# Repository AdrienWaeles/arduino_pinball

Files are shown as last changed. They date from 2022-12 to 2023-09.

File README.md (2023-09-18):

Dans le cadre des cours de robotique de 2ème année de classe préparatoire intégrée à Polytech Nice Sophia. Nous avons conçu et fabriqué un flipper de A à Z entièrement contrôlé par une carte Arduino.  

Ce GitHub rassemble nos rapports d'avancée hebdomadaire ainsi que tous les fichiers créés pour concevoir ce flipper.

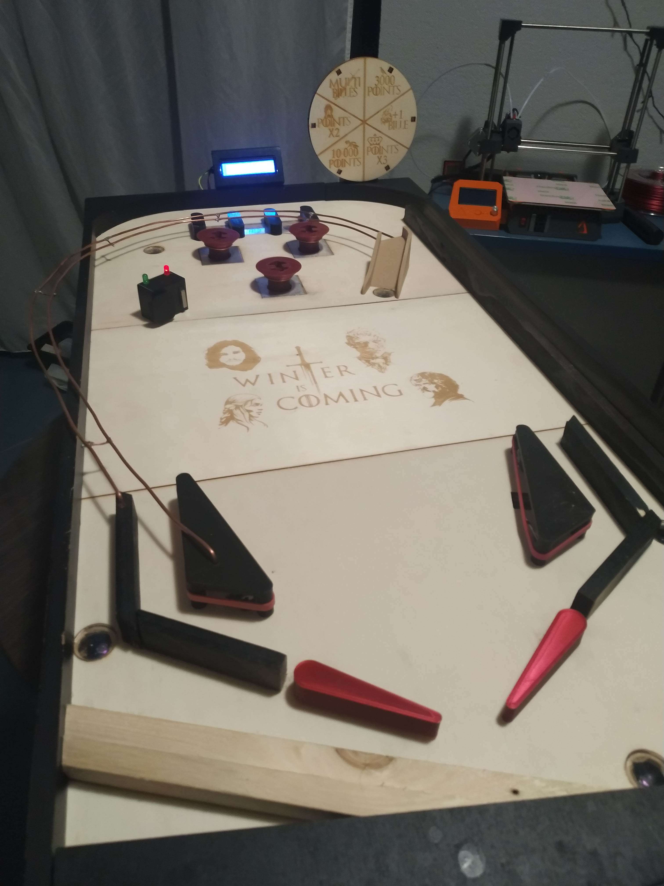
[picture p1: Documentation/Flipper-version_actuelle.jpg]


**Vidéo de présentation du projet** : https://youtu.be/dcDQBHgphmI

Cette première version a dû être réalisée dans un délai très court (moins de 3 mois) en pleine année scolaire. Ainsi nous avons du nous focaliser sur l'essentiel, mais ce projet a été conçu dès le début pour être évolutif et bénificiera d'améliorations prochainement.

Projet réalisé par Abderrahmane Redha et Waeles-Devaux Adrien.

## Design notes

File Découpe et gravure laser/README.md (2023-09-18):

Vous trouverez ici, tous les fichiers vectoriels (formmat SVG) conçus pour la découpeuse laser afin de réaliser les bordures et planches de jeu du Flipper.

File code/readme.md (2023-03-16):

Voici tous les programmes réalisés sur Arduino IDE pour tester nos différents éléments et la dernière version complète du jeu

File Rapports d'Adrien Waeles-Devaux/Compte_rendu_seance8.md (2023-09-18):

**Avant la séance :**

Nous avons profité des vacances pour passer quelques jours au Fablab afin d’assembler notre flipper. 
Pour cela avec l’aide de Frédéric Juan du Fablab nous avons commencé par coller les 3 fines planches sur la grande planche de jeu afin d’avoir l’emplacement de tous les trous à percer. Puis nous avons vissé toutes les bordures précédemment fabriquées.

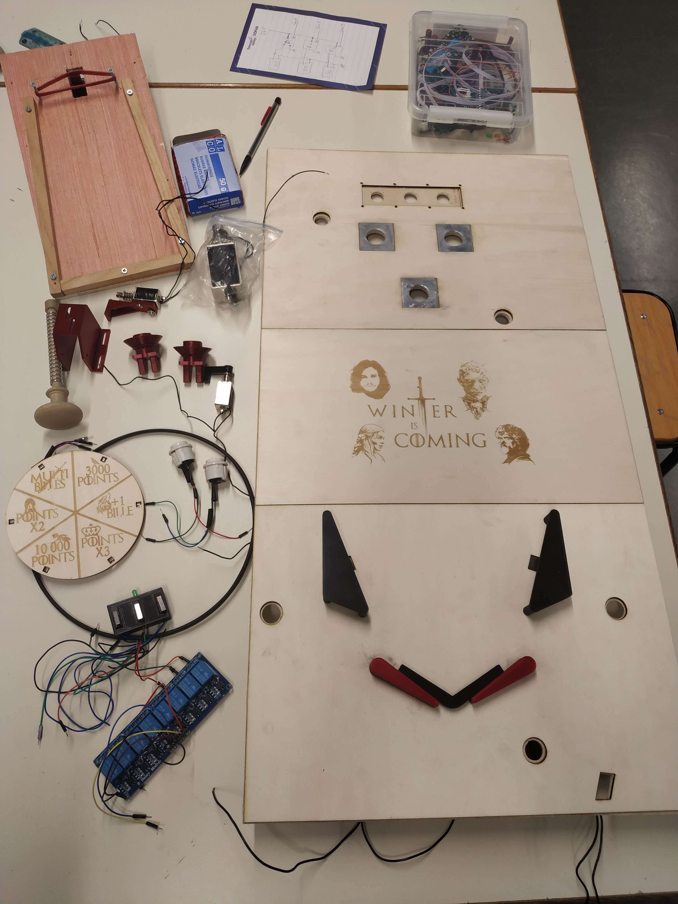
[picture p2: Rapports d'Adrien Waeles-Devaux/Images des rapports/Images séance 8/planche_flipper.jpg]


Pour déterminer l’inclinaison optimale de notre pinball nous avons utilisé un inclinomètre numérique. La plupart des pinball ont une inclinaison comprise entre 3° et 6°, après avoir testé différentes inclinaisons avec des cales de bois, nous avons choisi une inclinaison de 4°. J’ai ensuite mesuré et dessiné au crayon le support permettant d'incliner le pinball sur des morceaux de bois afin de les découper.

Il a fallu également effectuer un trou dans la bordure inférieure pour y insérer la poignée (modélisée en 3d avec un filetage pour pouvoir la démonter afin de l’insérer dans le trou). Cependant étant donné la force exercée par le ressort sur la bordure nous avons dû la renforcer par un morceau de bois plus haut à cet endroit.

Pour ramener la bille dans la zone de lancement lorsqu’elle est perdue par le joueur, nous avons vissé un solénoïde sous la planche et attaché à celui- ci un bras imprimé en 3D que j’ai modélisé. Ainsi lorsque celui-ci s'activera (donc quand la bille sera détectée par un capteur infrarouge de sortie de jeu), le bras du solénoïde poussera la bille pour l’envoyer au-dessus de la tige de la poignée de lancement. 

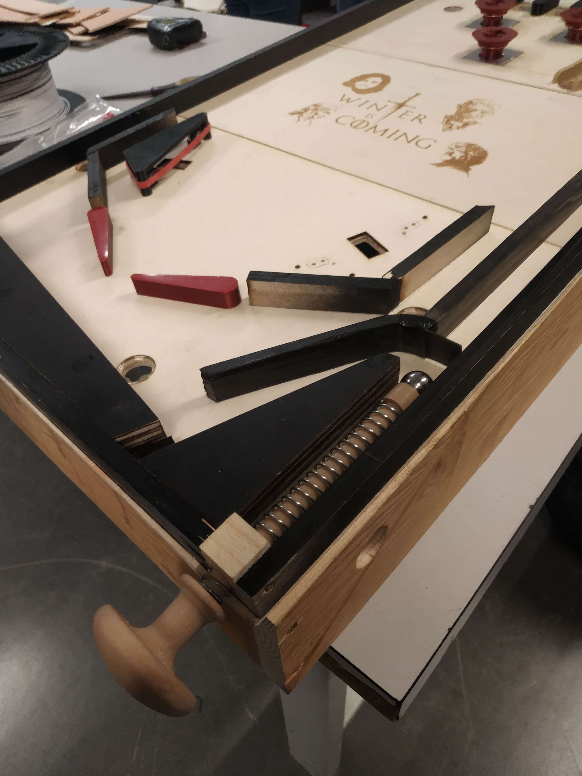
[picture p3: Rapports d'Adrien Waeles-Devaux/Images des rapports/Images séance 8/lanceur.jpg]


Voici le test de toute la zone de lancement en vidéo  :

https://youtu.be/IZiwfpQI0ls

Afin d’avoir tout le nécessaire pour l’assemblage de notre pinball, j'ai imprimé en 3D toutes les pièces modélisées et testées lors des séances précédentes 
J’ai notamment dû modifier l’épaisseur de la surface supérieure des tendeurs à élastiques des slingshots (pièces renvoyant la bille dans la direction opposée) car les pièces se courbaient en raison de la force de tension exercée par l’élastique  sur celles ci.
Il a fallu limer certaines pièces afin de s’assurer que le mouvement des pièces mécaniques (bumpers, flippers et slingshots) s’effectue sans trop de frottements.

J'ai passé plusieurs heures à régler les flippers (pièces frappant la balle contrôlées par le joueur) avec la bonne inclinaison. En effet, ceux-ci doivent être parfaitement disposés pour que le mouvement de rotation puisse s’effectuer correctement sans trop de frottements. J’ai imprimé une pièce donnant l’inclinaison utilisée dans la plupart des pinball (pièce noire sur photo ci dessous). Après de nombreux réglages il restait des blocages dans le mécanisme, j’ai donc dû limer les pièces plastiques afin de rajouter du jeu mécanique pour que les mouvements soient moins contraints.

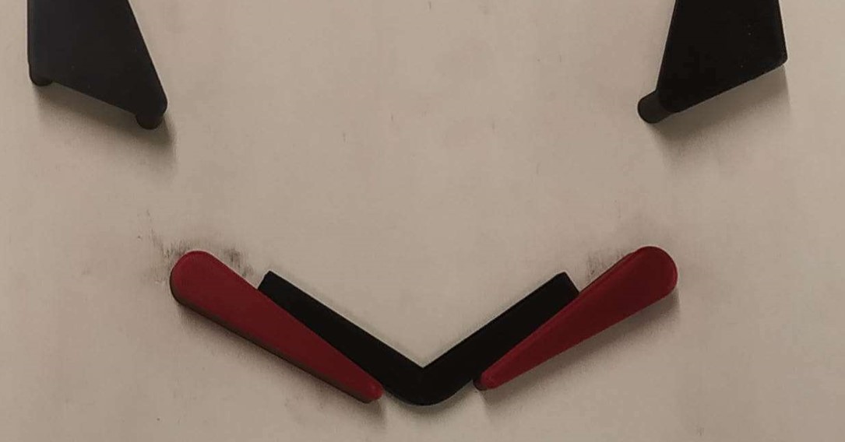
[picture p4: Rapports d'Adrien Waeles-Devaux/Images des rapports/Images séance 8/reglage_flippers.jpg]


Une fois toutes les pièces plastiques fixées, nous avons calibré la sensibilité de nos capteurs infrarouges. 
Puis je les ai vissé sous la planche. Il a fallu les positionner de façon à ce que les leds émettrices et réceptrices soient très proche de la plaque de plexiglass afin que lorsque la bille roule sur celle-ci, elle soit bien détectée. J’ai modélisé un support à la bonne hauteur sur lequel j’ai ajouté 3 trous pour que les résistances et les leds du circuit intégré du capteur s’emboîtent à l’intérieur sans être endommagées. Voici la pièce modélisée : 

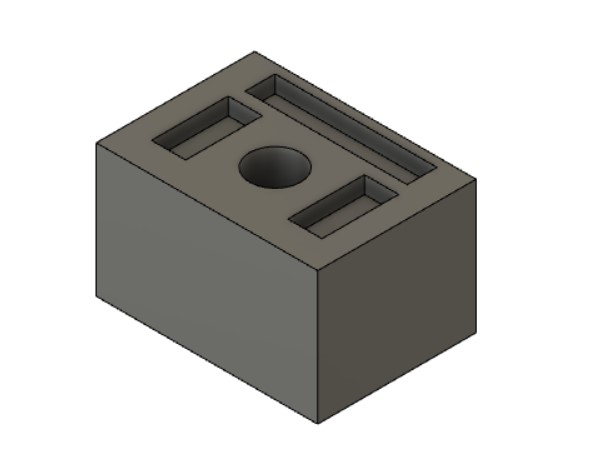
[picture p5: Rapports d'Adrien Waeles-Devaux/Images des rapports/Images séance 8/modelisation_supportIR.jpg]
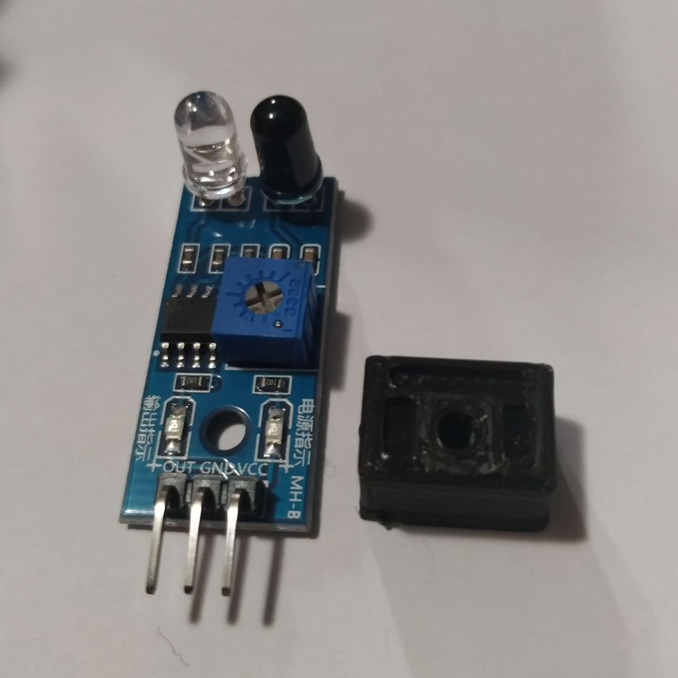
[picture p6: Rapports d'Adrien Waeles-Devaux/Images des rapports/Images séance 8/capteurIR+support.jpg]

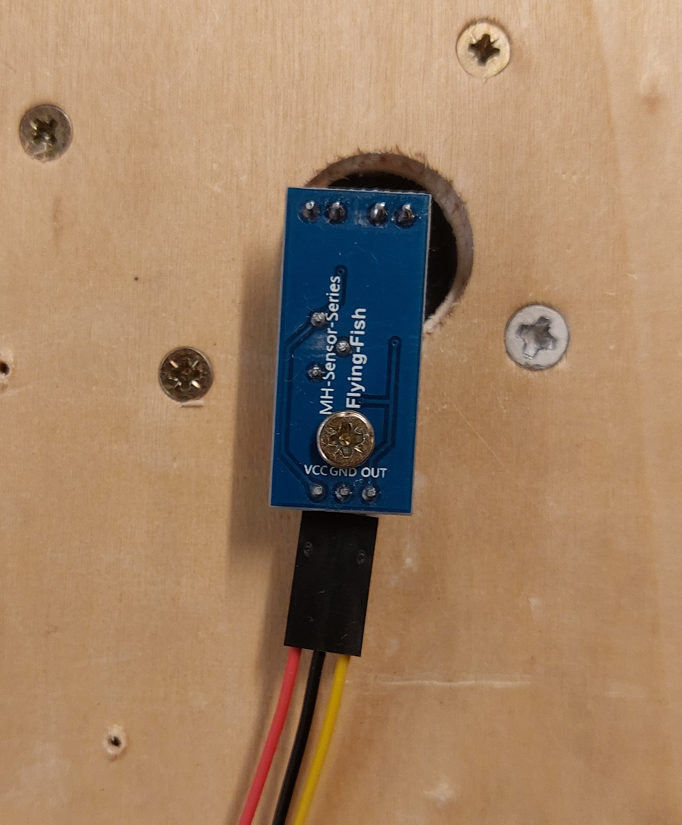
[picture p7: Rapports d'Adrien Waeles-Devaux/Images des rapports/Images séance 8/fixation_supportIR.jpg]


Précédemment j’avais également fabriqué par découpe et gravure laser un élément propre à notre flipper : la roue de la fortune. Cet élément du jeu permet de gagner un bonus au hasard indiqué par le clignotement d’une led associée au bonus en question. J’ai du alors découper un ruban de néo pixels afin de les disposer de façon circulaire dans les trous prévus et ensuite ressouder tous les néo pixels entre eux afin de pouvoir toujours les alimenter et contrôler avec seulement 3 fils.

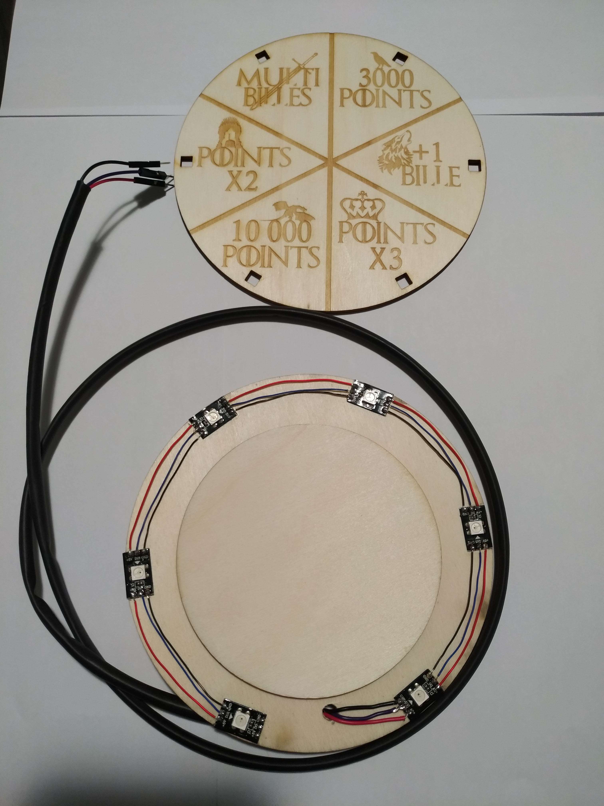
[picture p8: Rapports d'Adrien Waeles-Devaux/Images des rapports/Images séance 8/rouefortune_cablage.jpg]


Une autre étape très délicate dans l’assemblage de nos pièces était de fixer les micro interrupteurs permettant de détecter un impact sur l’élastique des slingshot. Tout d’abord j’ai testé différents microswitch afin de choisir les plus sensibles possibles.
Ensuite il a fallu les placer sous les slingshots. Comme constaté lors de la réalisation des prototypes, ils doivent être positionnés de façon à ce que la lamelle subisse une pression initiale exercée par l’élastique afin qu’ils se déclenchent au moindre contact. La pièce du slingshot ne permettant pas de régler facilement la position de ceux-ci, j’ai décidé de créer une autre pièce temporaire en copiant celle-ci et en ajoutant un trou à l’intérieur afin de pouvoir y passer des doigts pour placer l’interrupteur.

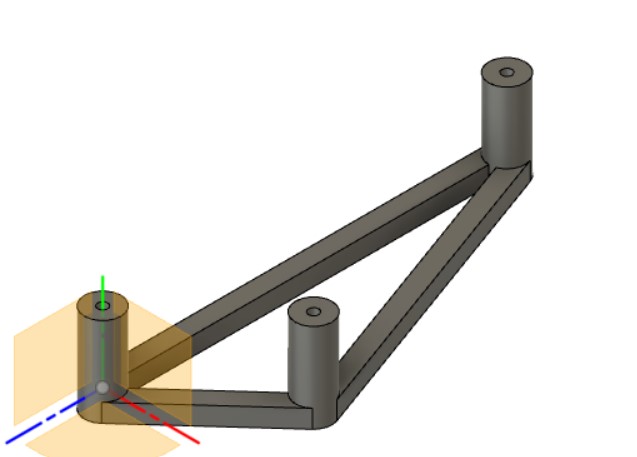
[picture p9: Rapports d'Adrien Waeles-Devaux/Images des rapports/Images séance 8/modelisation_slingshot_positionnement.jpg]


Pour les fixer j’ai modélisé et imprimé 4 supports permettant de les surélever à la bonne hauteur. Une fois la position optimale déterminée j’ai tracé le contour de ceux-ci sur la planche au crayon pour perçer des trous permettant de les visser.

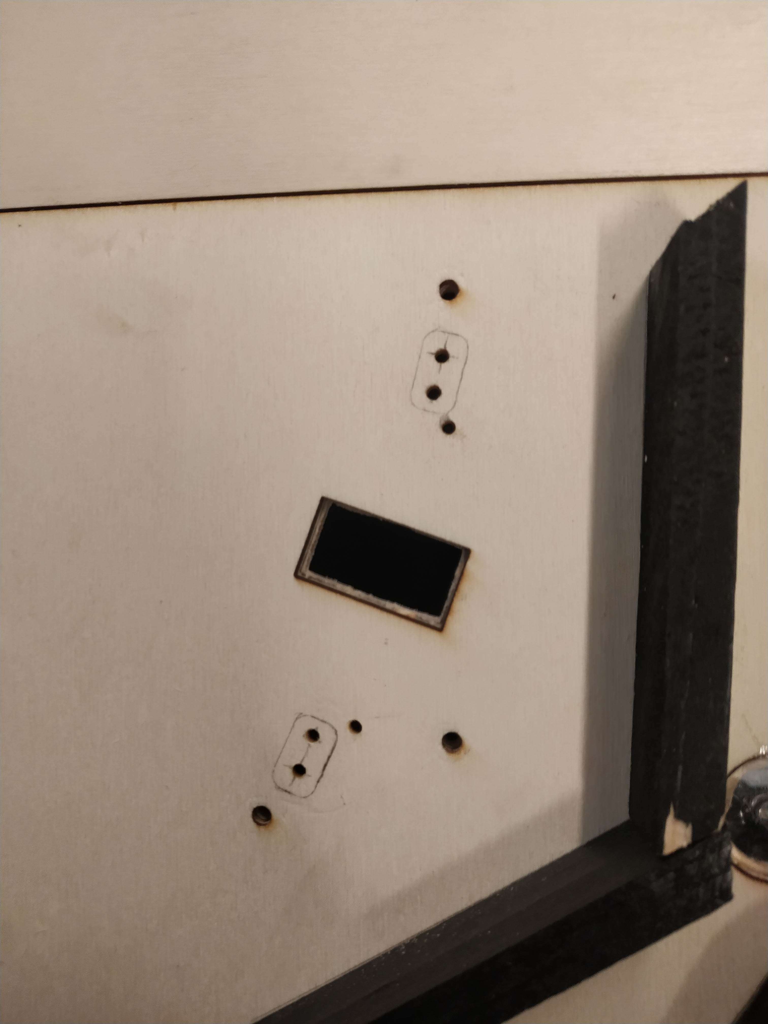
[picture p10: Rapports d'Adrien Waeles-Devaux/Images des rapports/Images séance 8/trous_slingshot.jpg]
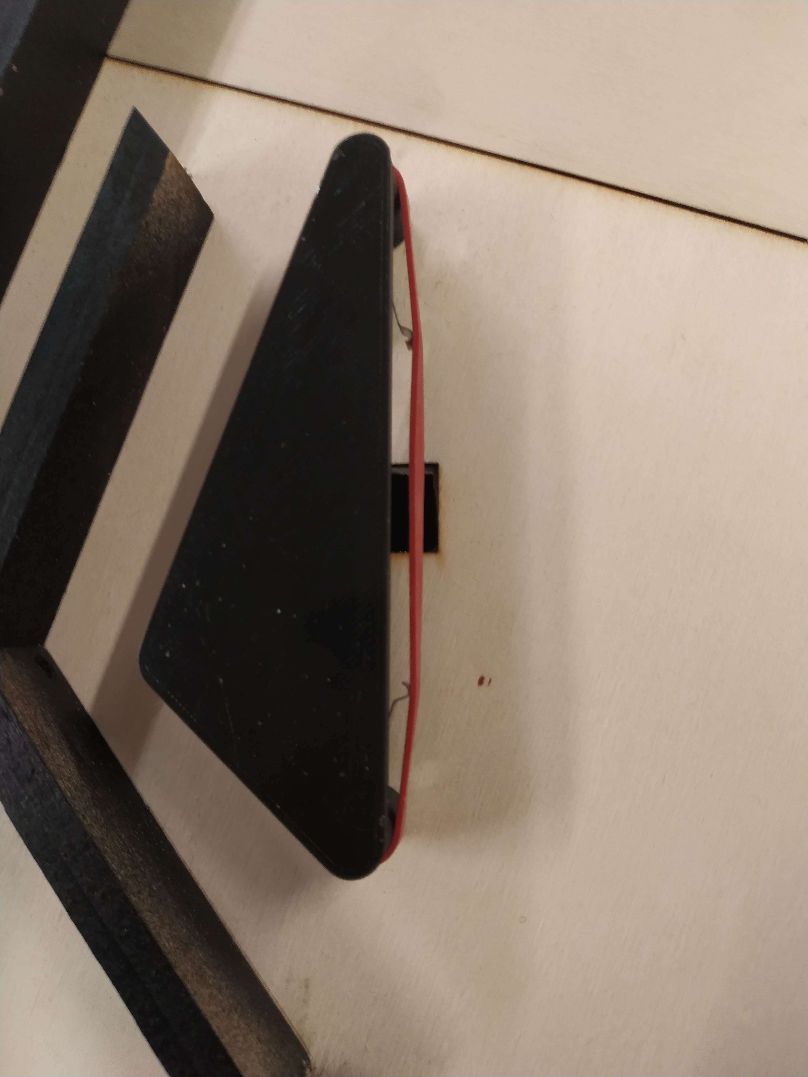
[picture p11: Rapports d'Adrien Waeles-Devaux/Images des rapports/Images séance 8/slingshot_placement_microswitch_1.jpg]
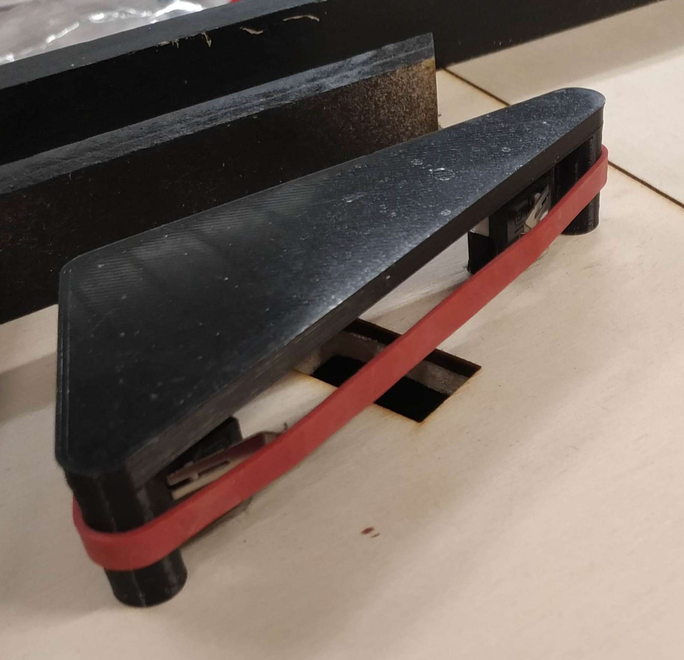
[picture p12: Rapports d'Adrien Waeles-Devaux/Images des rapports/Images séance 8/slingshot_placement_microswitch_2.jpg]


Durant le temps restant avant la séance j’ai fixé les différents composants électroniques sous la planche. Tout en réglant le convertisseur avec un multimètre pour qu’il transforme la tension de 24V en une tension de 5V en sortie afin d'alimenter l'arduino et les composants nécessitant 5V.

Finalement j’ai modélisé en 3D l'entrée de la rampe. J’ai effectué différents tests pour déterminer son inclinaison afin que la bille puisse atteindre le haut de celle-ci. Il restera à courber du fil électrique pour effectuer la suite de la rampe sur laquelle la bille va rouler. Étant donné que le capteur infrarouge, permettant de comptabiliser un passage sur la rampe dans le score, risque d’être déclenché lors d’un simple passage devant celle-ci. J’ai donc ajouté à la rampe 2 barrières d’une longueur de 20 mm afin d’éviter de comptabiliser par erreur un passage sur la rampe. 
De plus, si la bille repasse devant le capteur infrarouge un très bref instant après le premier passage, cela signifie que le joueur n’a pas réussi à l’envoyer en haut de la rampe et donc on n’ajoutera pas de points.

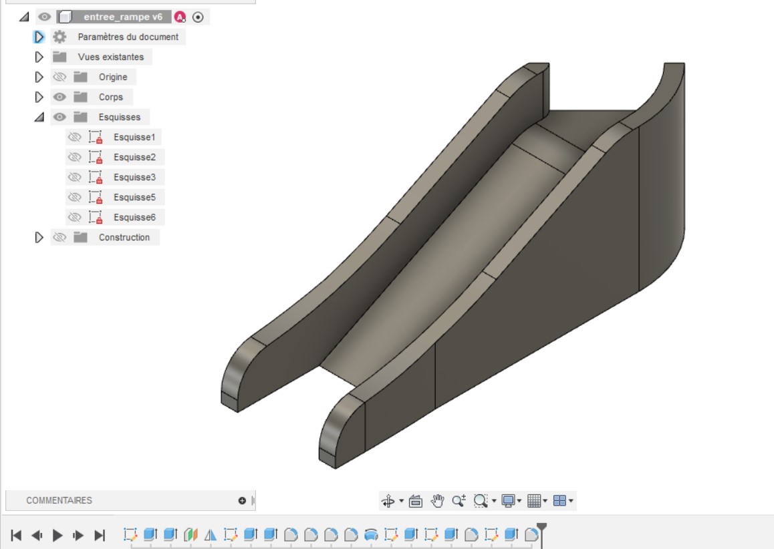
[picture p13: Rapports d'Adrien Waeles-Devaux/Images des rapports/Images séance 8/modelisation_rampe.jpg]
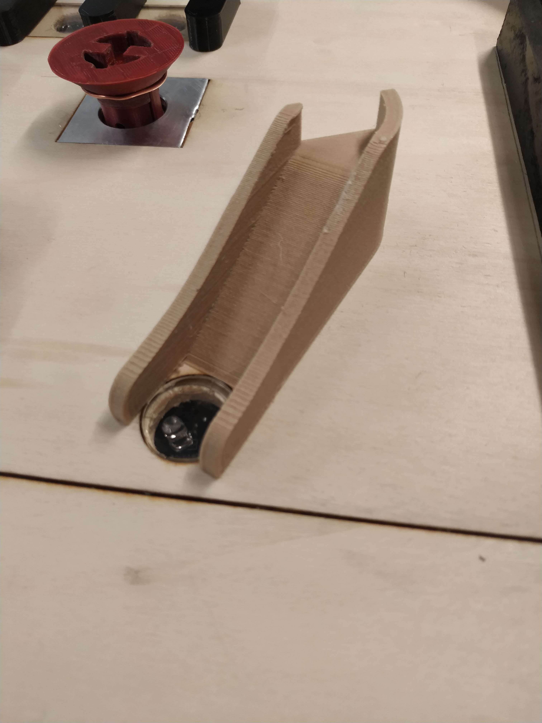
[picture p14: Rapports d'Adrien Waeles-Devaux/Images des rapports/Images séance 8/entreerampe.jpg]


Voici l’avancée du pinball avant la séance : 

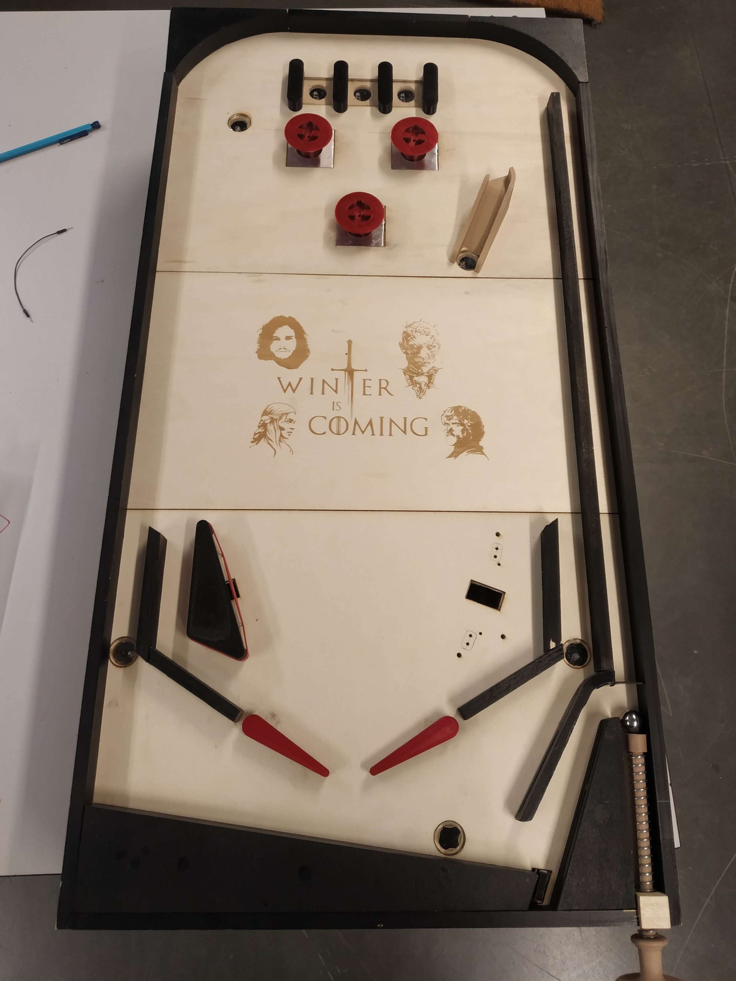
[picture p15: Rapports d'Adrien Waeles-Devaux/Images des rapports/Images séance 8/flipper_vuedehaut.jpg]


**Pendant la séance :**

Étant donné le peu de temps restant avant la date de présentation finale puisque tous les composants principaux maintenant fixés fonctionnent correctement mécaniquement, nous avons décidé de se consacrer pleinement en équipe au câblage des composants afin d’être sûr de pouvoir présenter une version fonctionnelle. Pour cela nous avons commencé par câbler tous les solénoïdes en parallèle afin d’avoir la même tension pour chaque solénoïde. 
Pour relier toutes les masses des solénoïdes entre elles nous avons utilisé 2 connecteurs wago à leviers. Un pour le haut du flipper et un pour le bas du flipper ,les deux étant reliés par un câble afin d’avoir une masse commune. 


Cela permet d’éviter de perdre du temps à effectuer des soudures et de pouvoir facilement débrancher un fil en cas de problème.

L’autre fil de chaque solénoïde est branché à un relais sur la broche Normally Open qui reçoit lorsque le circuit est fermé du 24V via l’alimentation.

Nous avons écrit un petit programme activant 3 solénoïdes en simultané afin de vérifier que tout fonctionne correctement. 
Puis un autre code pour activer les solénoïdes un par un toutes les secondes et vérifier qu’ils fonctionnent tous. 
Nous nous sommes alors aperçu que 2 solénoïdes ne fonctionnaient pas correctement. Nous devons donc encore vérifier les soudures et le branchement de ceux-ci.

Finalement j’ai aussi commencé à ajouter des attaches câbles afin de regrouper les fils passant au même endroit pour avoir un câblage plus ordonné et pouvoir nous y retrouver plus facilement.
Voici le dessous de la planche avec le câblage en cours d’installation (il reste encore de nombreux fils à brancher et à mieux ordonner les câbles)

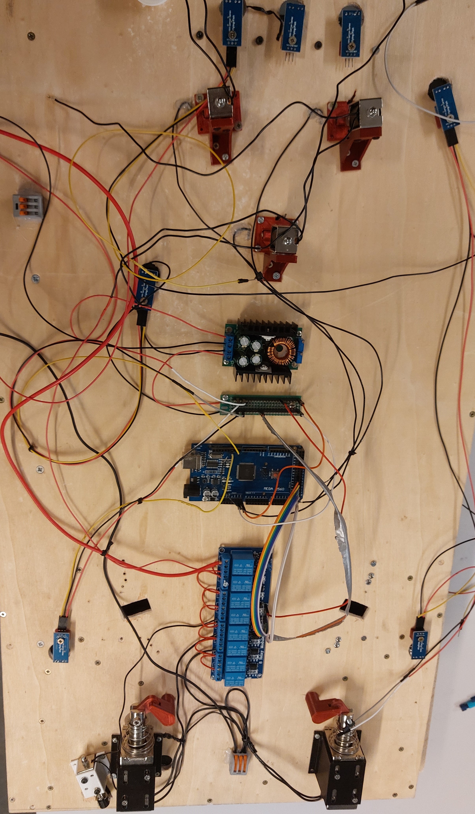
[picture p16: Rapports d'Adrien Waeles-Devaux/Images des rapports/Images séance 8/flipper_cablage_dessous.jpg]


**Étapes finales à réaliser :**

- Il nous reste désormais à terminer le câblage en branchant nos 8 capteurs infrarouges, les 2 boutons des flippers, les 7 microswitch des slingshots et cibles, l’écran, la roue de la fortune.

- Coller les cibles sur les microswitch, les assembler puis fixer le support sur la planche.

- Fixer l’écran et la roue de la fortune sur le flipper

- Finaliser la partie programmation, nous avions déjà réalisé des programmes pour tester chaque composant indépendamment, il faut désormais réaliser le programme complet permettant d’automatiser le fonctionnement d’une partie.

- Finir la fabrication de la rampe et la placer sur le flipper.

- Finitions et correction d’éventuels bugs

La suite du projet est consultable dans le rapport final de présentation disposé dans le dossier Documentation du GitHub.

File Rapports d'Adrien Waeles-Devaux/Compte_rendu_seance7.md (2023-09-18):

**Avant la séance :**

Nous avons finalisé la réalisation des bordures du flipper. Lors de la séance précédente nous avions déjà réalisé les bordures arrondies en transformant des modèles 3D en un fichier 2D svg utilisable avec la découpeuse laser. Pour rappel, chaque pièce devant mesurer 20mm de hauteur et la découpeuse laser étant actuellement limitée à des planches d’une épaisseur de 5mm, il a fallu coller 4 planches de 5 mm les unes sur les autres pour chaque pièce. 

Cette fois-ci nous avons découpé les pièces restantes du contour, qui sont 5 morceaux de bois coupés en ligne droite. 
Pour cela nous avons reporté les différentes mesures des contours de la maquette Sketchup sur nos morceaux de bois au crayon gris.
Sur cette capture d’écran de notre maquette on peut voir en haut à droite les pièces arrondies fabriquées à la séance précédente et en dessous les 5 morceaux de bois découpés juste avant cette séance : 

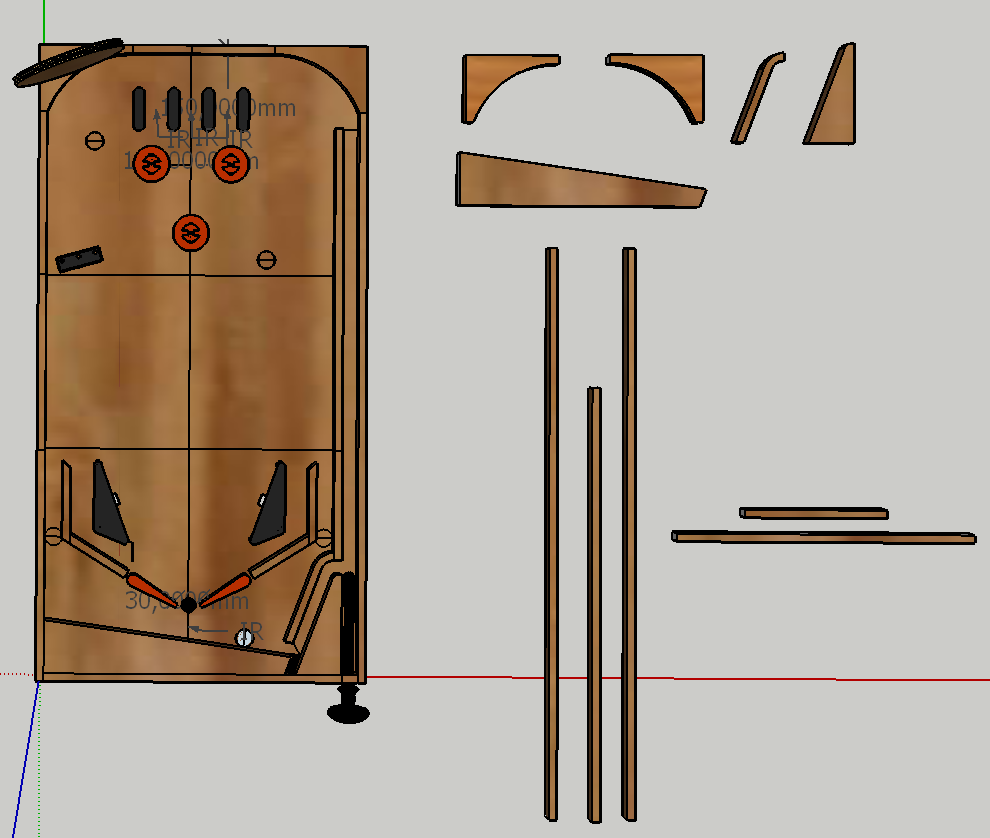
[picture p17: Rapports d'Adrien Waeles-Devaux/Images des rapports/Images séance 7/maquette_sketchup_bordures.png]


Il a fallu donc découper des morceaux de largeur 10mm de différentes longueurs et d’une hauteur de 20 mm. Puis pour des raisons de sécurité, les découpes ont été effectuées par un professeur au FabLab à la scie circulaire sur table.

Etant donné que certaines pièces arrondies ont légèrement brûlé lors de la découpe, nous avons décidé de peindre tout le contour en noir. J’ai alors appris à utiliser une bombe de peinture et retenu quelques conseils : secouer la bombe de peinture avant utilisation, commencer le mouvement avec la bombe en dehors de la surface à peindre afin d’avoir une peinture plus homogène et éviter des gouttes de peinture, purger la bombe de peinture en fin d’utilisation en la retournant et en pulvérisant pendant quelques secondes.

Voici le résultat avec toutes les pièces du contour disposées sur la planche (rien n’est encore vissé ou collé pour le moment, cela sera fait pendant la semaine des vacances) : 

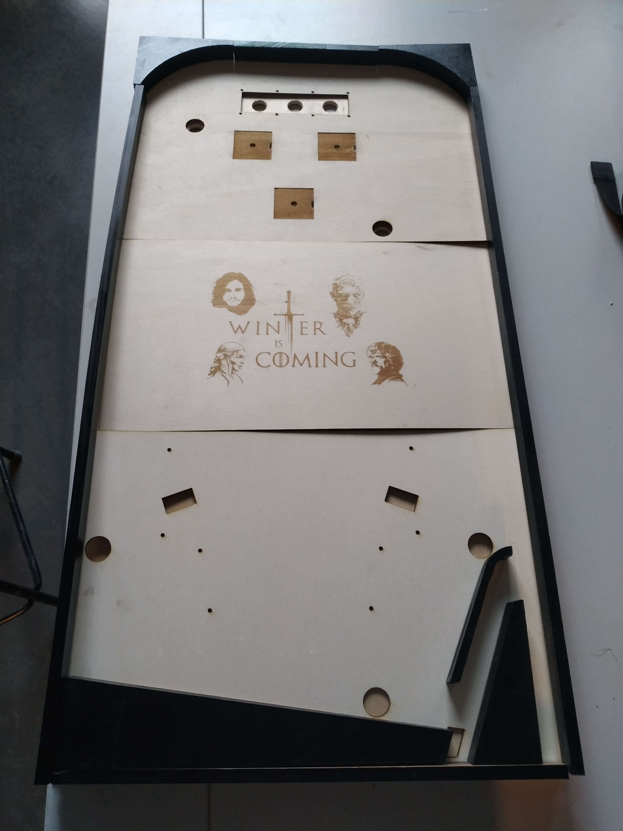
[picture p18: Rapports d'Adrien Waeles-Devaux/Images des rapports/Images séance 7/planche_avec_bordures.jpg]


Ensuite, j’ai utilisé le logiciel Fritzing pour réaliser un schéma du câblage du Flipper afin de s’assurer de tout brancher correctement et de gagner du temps le jour du câblage. 
Pour le moment j’ai cherché et importé tous les composants dans le logiciel et les ai disposés selon leurs emplacements sur notre flipper. Puis j’ai branché les solénoïdes aux relais. Cependant, nous nous sommes aperçus que les brancher en série risque d’engendrer une perte de puissance (3 solénoïdes pouvant être activés en même temps dans le pire des cas), il faudra alors les brancher en parallèle.

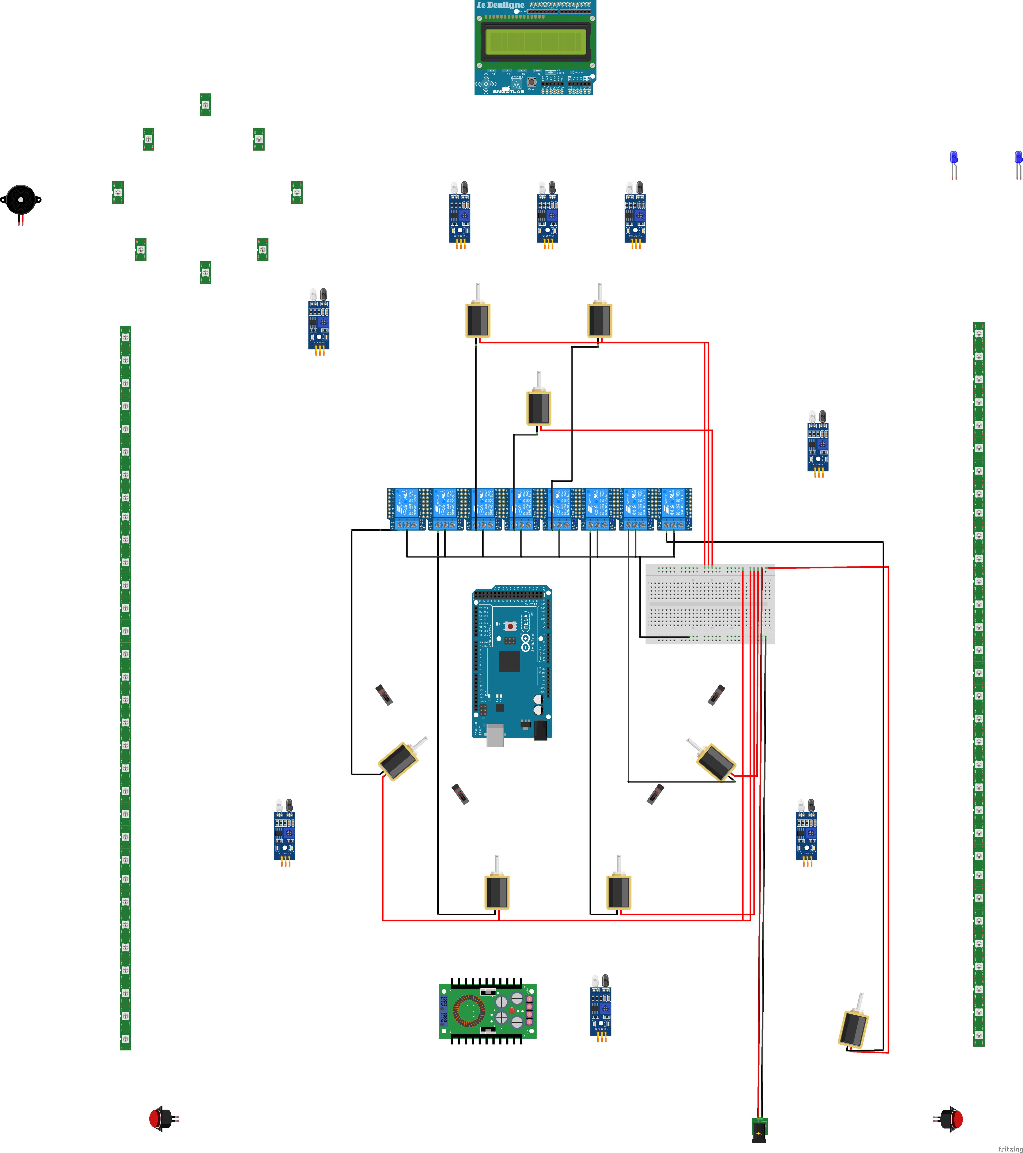
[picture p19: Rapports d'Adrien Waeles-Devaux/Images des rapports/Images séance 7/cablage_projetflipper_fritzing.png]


Comme chaque flipper est unique par sa décoration et ses éléments de jeu, je souhaitais intégrer un élément à notre flipper qui le distingue d’un flipper classique. J’ai alors imaginé un élément inspiré du jeu “la roue de la fortune” permettant de remporter lorsqu’elle s’active un bonus déterminé aléatoirement. 

Cette roue pourra être déclenchée par exemple lorsque toutes les cibles du jeu ont été touchées ou après que le joueur ait emprunté plusieurs rampes à la suite.

Pour fabriquer cette roue, j’utilise 6 néo pixels qui ont l’avantage d’avoir une colorimétrie RGB et d’éclairer avec une forte intensité tout en nécessitant seulement 3 fils pour tous les néo pixels. Ils vont permettre d’éclairer les différentes cases de la roue en fonction du bonus remporté. 
Je vais cependant faire face à une contrainte puisque nous n’avons pas de ruban circulaire de néo pixels. Je dois donc en découper 6 du ruban, les disposer en cercle puis les relier à nouveau entre eux en y soudant des fils afin de pouvoir toujours contrôler les 6 néo pixels avec un seul fil (en plus des 2 fils d’alimentation).

J’ai réalisé une petite animation avec un code Arduino pour avoir le résultat suivant : les leds vont s’allumer et s’éteindre successivement de façon à avoir un effet de lumière qui tourne autour de la roue. Puis cette animation va s’arrêter sur une led qui va clignoter pour indiquer le bonus remporté. 

J’ai également rajouté un buzzer qui effectue un son à chaque fois qu’une led s’allume. Pour que les néo pixels ne soient pas éblouissants, il est préférable de mettre des valeurs comprises entre 0 et 30 dans le code couleur RGB. 
Voici le résultat en vidéo :
https://youtube.com/shorts/hx9wgBHNqKs?feature=share

J’ai choisi de réaliser un assemblage de planches de bois découpées au laser en 3 planches de 3 mm. 
La première partie est celle visible par le joueur, c’est un cercle de 140mm sur laquelle sont inscrits les bonus à remporter et elle comporte 6 trous pour y placer les néo pixels. 
La 2ème est un simple cercle de la même taille sur lequel je vais coller chaque néo pixel en face de son trou présent sur la première pièce. Entre ces deux pièces, toujours avec la découpeuse laser j’ai fabriqué un 3ème cercle plus petit (100mm de diamètre) qui sera collé entre les deux et permettra de laisser la place pour passer les câbles reliant les 6 néo pixels en série.

Le tout sera fixé sur le rebord haut du flipper grâce à un support imprimé en 3D dans lequel je réaliserai un trou pour y passer les 3 câbles de branchement.

**Pendant la séance :**

Cette séance m’a permis de créer les pièces de bois de la roue de la fortune. 
Pour cela j’ai commencé par effectuer une esquisse sur papier pour déterminer le nombre de cases de la roue, l’emplacement des leds et les bonus que j’y inscrirai (j’ai donc cherché le mode de comptabilisation de points d’un vrai flipper).

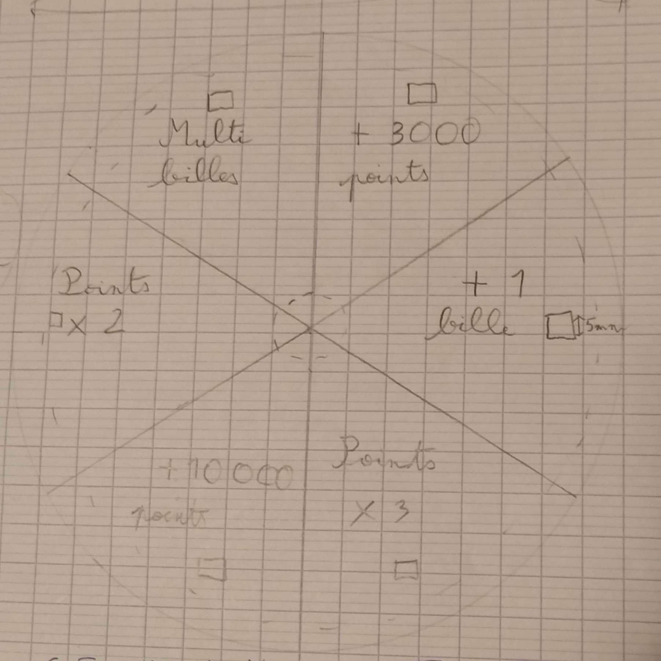
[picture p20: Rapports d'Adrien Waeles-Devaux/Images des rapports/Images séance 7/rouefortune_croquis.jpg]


Voici les bonus choisis : 

- Multi-Billes : déclenche un élément sur le plateau qui va relâcher 3 autres billes simultanément permettant au joueur de jouer avec plusieurs billes à la fois et donc de marquer plus de points.

- Points x2 / Points x3 : bonus multipliant les nouveaux points gagnés par le joueur par 2 ou 3 pendant un certain temps (le bonus sera par exemple désactivé au bout de 30 secondes).

- 3 000 points / 10 000 points : ajoute 3000 ou 10 000 points au score du joueur. Il sera possible dans le code de réduire la probabilité que l’on tombe sur la case 10 000 pour conserver la rareté de ce bonus important.

- +1 bille : rajoute un essai au joueur en lui offrant une bille supplémentaire qu’il pourra lancer depuis la zone de lancement une fois que les autres billes auront été perdues.

J’ai pour cela utilisé le logiciel Blender afin d’être plus efficace puisque je le maitrise bien mieux que Inkscape. Les cases sont séparées avec un angle de 60° par des rectangles de 2 mm de largeur. J’ai placé 6 carrés de côté 20 mm qui permettront de laisser passer les néo pixels.

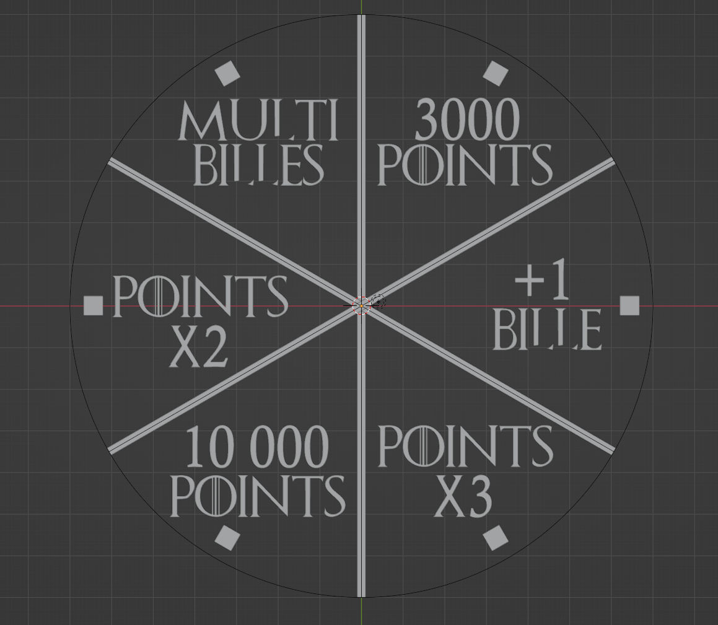
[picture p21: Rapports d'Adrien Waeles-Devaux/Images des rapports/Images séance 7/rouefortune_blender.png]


Pour ce qui est du texte j’ai utilisé une police d’écriture liée au thème du flipper. J’ai ensuite utilisé une extension nommée ‘freestyle svg export’ activable directement dans les paramètres du logiciel. Celle-ci permet d’exporter les contours d’un modèle 3D selon une vue en vecteurs dans un fichier svg. Pour l’utiliser il suffit de placer une caméra de rendu dans la vue désirée puis de lancer un rendu image avec l’extension activée.
Finalement dans inkscape, après avoir corrigé quelques erreurs d’exportation en svg avec l’aide de Redha Abderrahmane, j’ai ajouté un remplissage de couleur noir à l’intérieur des lettres afin qu'ils soient interprétés comme des gravures par le logiciel de découpe, puis j'ai placé des dessins vectoriels trouvés sur internet sur chaque case.

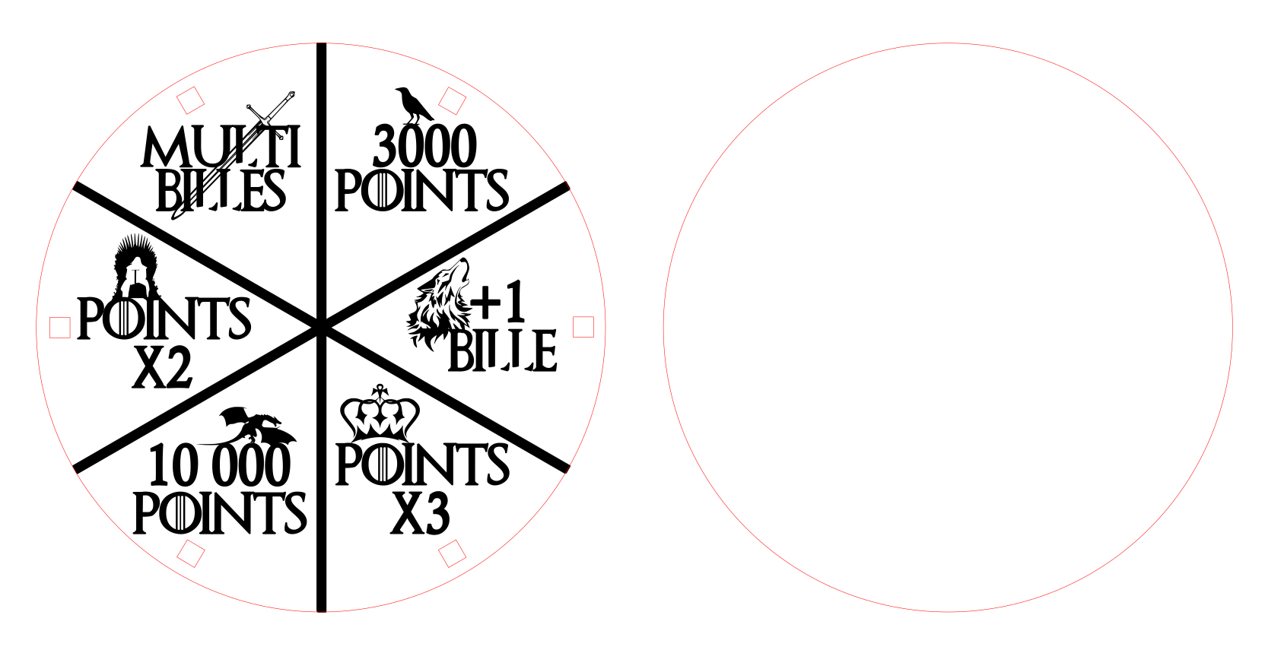
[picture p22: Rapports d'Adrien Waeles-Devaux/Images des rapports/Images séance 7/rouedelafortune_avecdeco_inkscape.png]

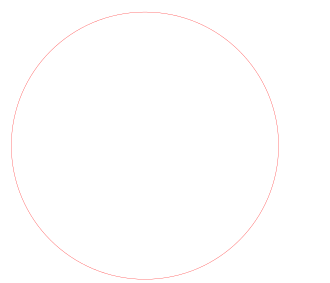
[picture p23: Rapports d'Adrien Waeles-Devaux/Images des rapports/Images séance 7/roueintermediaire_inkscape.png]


Et le résultat final après découpe et gravure au laser:

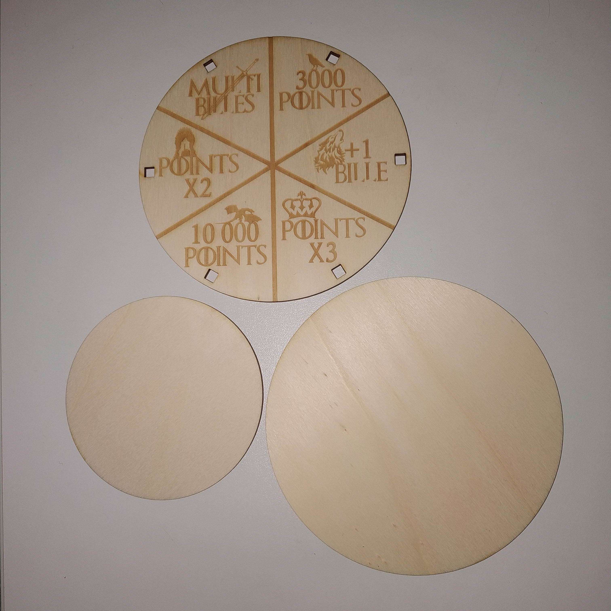
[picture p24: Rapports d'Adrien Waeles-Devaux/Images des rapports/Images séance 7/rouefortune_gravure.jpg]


J’ai également mis à jour la maquette sketchup en y ajoutant la roue de fortune avec l’image svg créée pour m’assurer du résultat : 
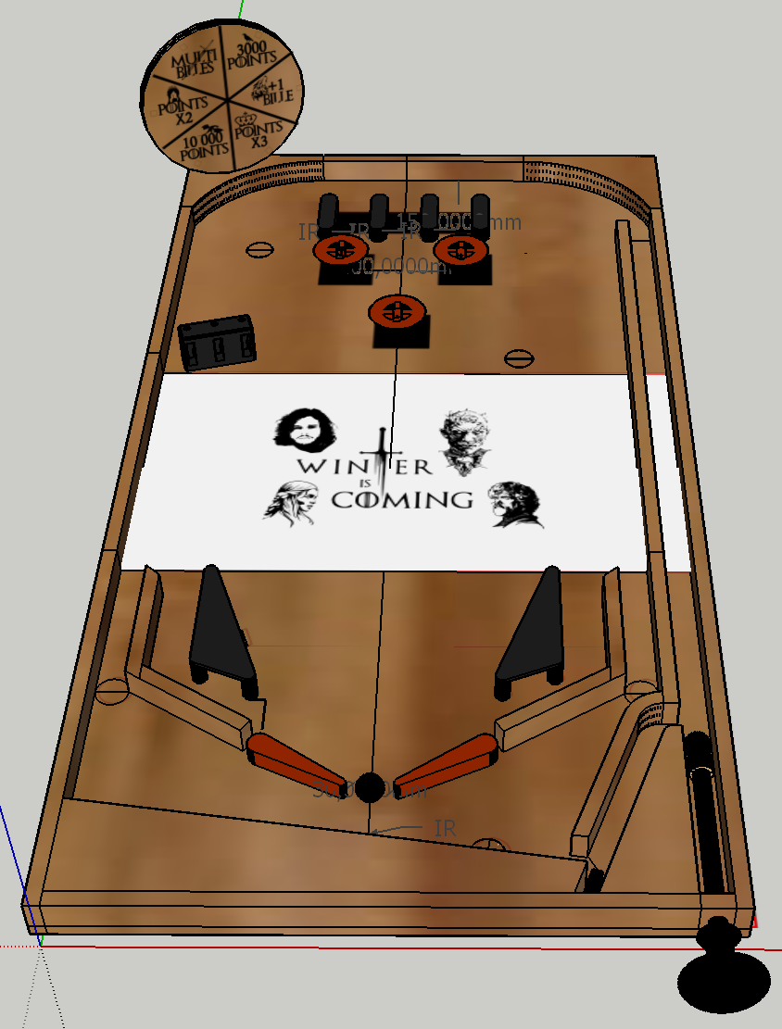
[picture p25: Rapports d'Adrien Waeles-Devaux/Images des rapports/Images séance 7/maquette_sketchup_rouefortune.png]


Finalement j’ai commencé à modéliser un support qui viendra se visser avec le reste des éléments sur la roue pour la fixer au-dessus d’un rebord du flipper.

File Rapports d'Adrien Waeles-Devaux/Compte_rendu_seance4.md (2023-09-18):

**Avant la séance :**

Pour commencer j’ai fixé un des 2 micro-interrupteurs du slingshot (pièce constituée d’un élastique destinée à renvoyer la bille dans la direction opposée, voir compte rendus précédents) sur la planche du prototype réalisé lors des séances précédentes. 



Cela a nécessité beaucoup de minutie car si la lamelle du micro-interrupteur n’est pas assez tendue par l’élastique, l’impact de la bille ne le déclenche pas (à moins de l’envoyer avec une très grande vitesse). 
Et si elle est trop tendue, la lamelle ne revient plus à sa position initiale après l’impact en raison de la pression exercée par l’élastique (le bouton de l’interrupteur est alors constamment enfoncé). 

Il a fallu surélever légèrement le micro-interrupteur de la planche pour que la bille frappe celui-ci à hauteur de son centre de gravité afin qu’elle exerce une force maximale sur la lamelle. Provisoirement cela a été fait avec 2 petits écrous. Sur la version finale il pourra être utile de fabriquer une petite pièce adaptée. Sur le slingshot final il y aura un micro-interrupteur de chaque côté de l’élastique afin d’avoir la même sensibilité de détection d'impact des deux côtés. 

Après de nombreux tests pour fixer le micro-interrupteur de manière optimale voici le résultat : https://youtube.com/shorts/6lyibMg2PRw

J’ai ensuite réalisé un prototype d’un bumper à l’aide d’un solénoide (KK-0630B, 24V, 600mA, 10mm de course, 8Newtons) sur la planche de prototypage que j’avais utilisé pour créer le slingshot. Pour cela je me suis aidé de ce design : https://www.thingiverse.com/thing:3286052. Le bumper est constitué de deux pièces, le cône qui s’abaisse sur la balle et une pièce fixe qui permet de maintenir le cône droit, dans lequel la première pièce va coulisser.



J’ai importé ces pièces dans un logiciel de modélisation 3D, et j’ai modifié l’écartement entre les 2 pattes qui viennent se serrer sur le solénoïde pour pouvoir y fixer le nôtre, qui est bien plus petit que celui utilisé par le créateur des fichiers 3D.



Le fonctionnement est le même que celui expliqué dans le compte rendu de la séance 3 : la pièce conique qui est attachée au solénoïde va s'abaisser sur la balle pour la pousser dans la direction opposée. Pour fixer le bumper à la planche, j’ai percé un trou dans le prototype et à partir des dimensions mesurées, j’ai modélisé et imprimé une équerre qui permet de fixer le solénoïde sous la planche. 



Remarque : l’équerre sera modifiée par la suite étant donné en raison d’une erreur d’orientation de la pièce lors de la modélisation.

Voici la démonstration en vidéo : https://youtube.com/shorts/1k2h37szUpM

**Durant la séance :**
Après avoir présenté l’avancée de notre projet lors d’un oral de 10 minutes. Nous avons commencé à réaliser le système permettant de détecter le contact de la bille sur le bumper. Pour cela, nous avons coupé une fine plaque de métal au Fablab aux dimensions du bumper qui sera encastrée dans la planche juste en dessous de celui-ci. Nous avons trouvé un fil rigide que nous allons insérer dans une rainure sur l’extrémité haute de la pièce du bumper. Ainsi quand la bille roulera sur la plaque métallique et qu’elle sera en contact en même temps avec le fil, le bumper sera déclenché et l’arduino recevra un signal permettant d’ajouter des points au joueur.

J’ai pu remarquer que le mouvement vertical de la pièce conique du bumper imprimée en 3d est interrompu par la planche. Donc on ne profite pas de l'entièreté de la course qu'offre le piston du solénoide. Et cela puisque les pattes de la pièce conique ne sont pas assez longues. J’ai alors modifié la modélisation 3d pour prolonger celles-ci afin que le bumper puisse avoir une position initiale plus haute et donc pour que le solénoïde puisse effectuer sa course entièrement.
J’en ai profité pour ajouter la rainure qui permettra d’y insérer le bout de métal. 

Finalement, je me suis intéressé au fonctionnement d’un écran lcd qui permettra d’afficher le score du joueur tout au long de la partie et éventuellement des messages relatifs au déroulement de la partie. L’écran lcd utilisé est “QAPASS 1602A”. Étant donné que nous avons besoin de garder un grand nombre de broches libres pour les nombreux composants de notre flipper, afin de réduire le nombre de connexions que nécessite un afficheur LCD, nous utilisons une interface série I2C (modèle HW-061) qui fait le lien entre l’arduino et l’afficheur. 



Afin de connecter cette interface à l’écran, j’y ai soudé une bande de broches dans laquelle j’ai inséré les 16 connecteurs de l’interface. Le programme pour faire fonctionner l’écran et y afficher le nombre de points sera réalisé avant la prochaine séance.



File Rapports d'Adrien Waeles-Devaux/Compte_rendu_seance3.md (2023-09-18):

En arrivant à cette séance, nous avions reçu de nouveaux solénoïdes: (modèle KK-0630B, 24V, 8 Newton, 400 mA, 10 mm de course) plus puissants que les solénoïdes que nous utilisions pour les slingshots. Ces solénoïdes seront utilisés pour créer nos 3 bumpers. Ce sont des pièces que l’on retrouve sur tous les flippers qui sont situées en haut de la table de jeu disposées en triangle et qui permettent de marquer des points. Leur fonctionnement est le suivant, lorsque la bille touche un bumper, le joueur va marquer des points et la bille va être renvoyée dans la direction opposée grâce à un mécanisme qui s'abaisse sur la bille et remonte immédiatement ensuite (voir schéma ci-dessous).



Ceux-ci sont disposés assez proches les uns des autres de manière à ce que la bille fasse des aller retours d’un bumper à un autre plusieurs fois afin de marquer des points à la suite. 

Ainsi durant cette séance nous avons effectué de nombreuses recherches sur les différents mécanismes possibles pour les fabriquer. Pour les réaliser, nous avons décidé d’utiliser un solénoïde placé verticalement sous la planche (maintenu par une équerre) et attaché à une pièce plastique passant à travers la planche qui va s'abaisser sur la balle lorsqu’il y a un contact. Pour détecter ce contact, nous pensons utiliser du scotch de cuivre collé en dessous des bumpers (utilisé comme conducteur) et créer un petit anneau métallique relié au 5V de l’arduino et attaché à la partie haute du bumper. Ainsi quand la bille métallique sera en contact à la fois avec le scotch de cuivre et l’anneau métallique, la bille fermera le circuit . La lecture du courant dans ce petit circuit sur une entrée digitale de l’arduino permettra de détecter lorsque le circuit est fermé. Suite à ce contact ou pourra alors incrémenter les points du joueur et enclencher le solénoïde correspondant pour renvoyer la balle.  

Nous avons trouvé ce modèle 3d qui correspond exactement à ce que l’on souhaite faire : https://www.thingiverse.com/thing:3286052.
Nous devrons cependant l’adapter pour que les dimensions des pièces et des trous permettent d’y fixer nos solénoïdes qui ne sont pas les mêmes.



Nous avons mis un certain temps à trouver une alimentation pour ces nouveaux solénoïdes, en effet la première alimentation utilisée indiquait une tension de 24V alors que sa tension réelle mesurée avec un multimètre était de 60V. Nous avons finalement trouvé une alimentation délivrant une tension réelle de 24V et un courant de 2.2A, ce qui nous a permis de tester les nouveaux solénoïdes reçus. Cependant il y a un mauvais contact au niveau du connecteur de la nouvelle alimentation, nous devons donc trouver une solution à ce problème d’ici la prochaine séance. 

Nous avons aussi rencontré une petit difficulté avec les nouveaux solénoïdes, la documentation de ceux-ci affichait une course de 10mm mais en réalité les moteurs ne pouvaient effectuer qu’un mouvement de 5mm, pour régler cela il suffisait de retirer un des 2 écrous et caoutchoucs restreignant la course du solénoïde présents au bout de la tige du solénoïde.

J’ai ensuite pu tester et imaginer le fonctionnement d’un bumper à l’aide d’un de ces solénoïdes. Voici le résultat avec cette petite vidéo montrant simplement comment celui-ci fonctionnera (pour le moment le solénoïde est déclenché manuellement). Le circuit électronique est toujours le même que pour le solénoïde des slingshots à l’exception que l’alimentation utilisée fourni une tension de 24V au lieu de 12V) : https://www.youtube.com/shorts/0AeFL3rPPoE.

Pour les prochaines séances, je vais essayer d’imprimer des pièces en plastiques permettant de fixer ces solénoïdes sous la planche et d’adapter les modélisations 3D des bumpers à nos solénoïdes pour pouvoir effectuer des premiers tests.

En fin de séance, j’ai décidé du placement des micro-interrupteurs sur le prototype du slingshot créé à la séance précédente et j'ai trouvé des vis à bois adaptées permettant de viser directement les micro-interrupteurs sur la planche sans nécessairement avoir besoin de perçer des trous.

Finalement j’ai modifié le fichier 3d de la poignée utilisée pour le lanceur manuel de billes afin d’y ajouter une tige qui rentre dans le ressort. Nous avions initialement prévu de coller à la poignée une tige en bois mais n’ayant pas trouvé de tige aux bonnes dimensions et pour avoir un ensemble poignée + tige plus robuste nous allons l’imprimer en plastique sur la même pièce que la poignée. Le petit cube au bout de la tige permettra d’y emboîter une autre pièce qui va frapper la bille. Remarque : la pièce sera peut être encore modifiée pour la rendre plus facile à imprimer en 3D et éviter l’impression de supports. Voici la nouvelle poignée modélisée en 3d : 



Après la séance, j’ai reçu un solénoïde qui servira à faire bouger les flippers (modèle KK64B, 24V, 2A, 20mm de course, 65Newton). J’ai pu le tester avec l’alimentation de 24V et voici le résultat en vidéo ( le code utilisé est le même que celui de la première séance (disponible sur le github) : lorsque le bouton est appuyé une tension est envoyée au solénoïde pour l’activer jusqu’à ce que le bouton soit relâché). https://www.youtube.com/shorts/n7QumtdJi2Y

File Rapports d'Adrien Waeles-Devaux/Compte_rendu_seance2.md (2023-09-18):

**Avant la séance :**

À partir de la liste de composants établie au début du projet dans le cahier des charges, nous avons cherché les références des composants à acheter pour le pinball, notamment en faisant des recherches sur la force en newton et le voltage nécessaire pour exercer suffisamment de force sur la balle (voir liste des composants). Puis nous nous sommes rendus dans plusieurs magasins de bricolage afin de trouver des ressorts et élastiques, pour pouvoir avancer le projet. Le ressort permettra de fabriquer le lanceur manuel de bille.

Après avoir reçu des élastiques et des billes adaptés au projet, j’ai créé un prototype d’un slingshot en perçant une planche et en y fixant des clous. Cette pièce située au-dessus des flippers permet de faire rebondir la balle sur un élastique lorsque celui-ci est touché afin de ramener la bille dans la zone de jeu. Elle est constituée d’un élastique tendu auquel sont collés des micro-interrupteurs et sous la planche se trouve un solénoïde. La référence du solénoïde actuellement utilisé est : JF-0730B (12V, 5N, 10mm de course).



Le fonctionnement est le suivant, lorsque la bille vient taper l’élastique celui-ci exerce une pression qui va déclencher au moins un des 2 interrupteurs disposés de chaque côté de l’élastique, une fois le signal reçu on enclenche immédiatement le solénoïde pour tendre l’élastique dans l’autre sens avec une petite pièce en plastique passant à travers la planche afin de repousser la balle. Voici la pièce en question modélisé en 3d :



J’ai testé différents micro-interrupteurs afin de choisir les plus sensibles pour que le slingshot se déclenche même si la balle arrive dessus avec une faible vitesse. Pour avoir une meilleure sensibilité, une astuce consiste à placer le bouton de façon à tendre légèrement l’élastique avec celui-ci sans que cela enclenche l'interrupteur. Finalement j’ai modélisé et imprimé une équerre permettant de fixer le solénoïde en dessous de la planche.

Pour la création des cibles du pinball, nous avons modélisé sur Fusion 360 un support permettant d’y loger 3 micro-interrupteurs et 3 leds associées à chaque interrupteur qui s’allumeront lorsque leur interrupteur associé est touché. 3 trous en haut de l'objet permettent d'y insérer des leds, en dessous de la pièce, des trous permettent de passer les câbles de chaque led et interrupteur et 2 autres permettent de fixer le support à la planche.




Finalement j’ai modélisé en 3d une poignée sur Blender. Cette poignée servira à créer le lanceur manuel de bille. Le lanceur sera constitué d'une tige en bois associée à un ressort avec d'un côté la poignée sur laquelle on va tirer pour propulser la balle en haut du pinball. 




**Durant la séance :**

Dans un premier temps, j’ai adapté le code réalisé lors de la première séance qui servait à déclencher les solénoïdes des flippers avec boutons. Le fonctionnement des slingshots est en effet très similaire, la seule différence entre les 2 programmes est que pour les slingshots après le déclenchement du solénoïde celui-ci doit se rétracter immédiatement même si l’interrupteur reste enfoncé pendant plusieurs millisecondes. Ainsi dans le programme, le solénoide est déclenché seulement lorsque la valeur renvoyée par l'interrupteur passe de l'état HIGH à LOW (mais pas l'inverse car le solénoide ne doit pas se réenclencher lorsque l'interrupteur est relaché). (le code commenté est disponible sur le github). 

Puis nous avons fixé le solénoïde en dessous de la planche du prototype à l’aide de petites vis et de l’équerre préalablement imprimée en 3d (le solénoide sera mieux fixé à la planche par la suite, ceci reste un prototype). 



Le bras du solénoïde doit être placé un peu en retrait de l'élastique afin d’éviter que la bille ne frappe la pièce en plastique au lieu de l’élastique ce qui ne déclencherait pas les micro-interrupteurs mais tout en restant le plus proche de celui-ci pour que le mouvement du solénoïde tende l'élastique au maximum.

Il a fallu ainsi réaliser de nombreux tests pour trouver le positionnement optimal du bras du solénoïde et des micro-interrupteurs et la tension de l'élastique à appliquer pour que la balle déclenche correctement l'interrupteur (il y en aura 2 sur la version finale) et que le solénoide tende suffisamment l'élastique. Le prototype nous permet ainsi de vérifier que tout fonctionne et de déterminer le placement de chaque élément du slingshot afin de fabriquer plus tard une pièce avec les bonnes mesures. Voici une démonstration du prototype avec une bille : https://youtu.be/Ld9HjYVpliU

Comme on peut le voir lorsque que le micro-interrupteur est bien placé, le choc de la bille sur l’élastique déclenche bien le slingshot et cela même si la bille arrive avec une vitesse peu élevée sur le slingshot. Le prototype semble donc fonctionner cependant le slingshot ne renvoie pas la balle avec beaucoup de force et cela en raison notamment de la course du solénoïde de seulement 10mm qui ne tend pas suffisamment l’élastique. Pour améliorer cela on pourra éventuellement par la suite tester avec un autre solénoïde (ayant une course plus grande ou plus de force pour tendre l'élastique plus efficacement) ou changer la pièce par un système de levier.

En fin de séance, j'ai réfléchis à la meilleure manière de fixer les micro-interrupteurs et recherché des vis adaptées afin de pouvoir finaliser le prototype du slingshot. Puis nous avons commencé à imaginer la conception du lanceur de billes en cherchant une tige en bois adaptée aux ressorts que nous avions trouvé.

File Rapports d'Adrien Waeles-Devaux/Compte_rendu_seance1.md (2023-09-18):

Contenu de cette séance : Flippers imprimés en 3D, test de fonctionnement d’un solénoïde avec bouton et détection de passage d’une bille avec un capteur infrarouge.

Avant la séance : 
Nous avons modélisé en 3d deux pièces pour créer un prototype de flipper, puis je les ai imprimé en 3D afin de pouvoir effectuer des tests le jour de la séance et adapter les pièces en conséquence. La première pièce ci-dessous étant le flipper gauche qui sert à renvoyer la balle sur la planche.  La deuxième pièce (la plus petite sera cachée sous la planche et fixée au moteur), elle permet de transformer le mouvement linéaire d’un solénoïde en un mouvement de rotation. Il faudra ajuster prochainement les dimensions et la forme de cette dernière pièce pour l’adapter au solénoïde choisi.





Durant la séance :
Test de fonctionnement du solénoïde JF-0730B (12V, 1A, déplacement de 10mm).
Étant donné que le solénoïde nécessite d’être alimenté avec une tension de 12V, il nécessite une alimentation externe, afin de ne pas endommager la carte arduino, pour cela j’ai ajouté au circuit un relais commutateur. 
Documentation du relais commutateur JQC-3FF-S-Z : 



Le relais commutateur se comporte comme un interrupteur qui est commandé par l’arduino. Ainsi lorsque l’interrupteur est fermé le solénoïde sera alimenté par l’alimentation externe (ici alimentation 12V) et lorsque l’interrupteur est ouvert le solénoïde n’est plus alimenté. Pour ouvrir ou fermer l’interrupteur on envoie un signal numérique depuis l’Arduino. Ainsi on évite de faire trop chauffer le solénoide puisqu’il n’est alimenté que lorsque l’on appuie sur le bouton.

Le programme réalisé est le suivant : 



Voici le fonctionnement de ce premier test en vidéo :
https://www.youtube.com/watch?v=6iraHV_b1UE

Résultat des tests et des recherches : le petit solénoïde 12V utilisé ne semble pas suffisant pour faire bouger avec assez de force les flippers, la balle risque de ne pas atteindre le haut du flipper. 
Il semble qu'un solénoïde de 24V serait idéal. Cependant ce petit solénoïde peut être utilisé sans problème pour les slingshots qui nécessitent une force moins importante.

Remarque : d’après mes recherches, il est nécessaire d’avoir une diode branchée à chaque solénoïde car sans cela lorsque l’on envoie du courant au solénoïde puis qu’on coupe le courant pour qu’il revienne dans sa position initiale, le courant risque d’être renvoyé dans le sens inverse ce qui parasite les informations reçues par l’arduino et fait chauffer encore plus le solénoïde mais cette diode est déjà intégrée au relais.

Finalement, j’ai commencé en fin de séance à réfléchir à l’utilisation des capteurs infrarouges. Les capteurs infrarouges seront utilisés pour savoir où la balle est passée sur le pinball, en fonction de ces informations il sera alors possible de comptabiliser des points, déclencher certains moteurs ou même allumer des leds. Le câblage est tout simple, le capteur est relié au +5V et à la masse de l’arduino et il suffit ensuite de relier un dernier câble sur sur une patte digitale de l’arduino et du capteur. En effet, pour ce projet on a seulement besoin de savoir si une balle est passée ou non, donc la lecture d’un signal numérique suffit. J’ai créé ce simple programme afin de compter le nombre de passages devant un capteur :



J’ai rapidement constaté qu’il ne sera pas possible d’utiliser la fonction de temporisation delay() dans notre algorithme sous peine de mettre tout le programme en attente. En effet, certains éléments tels que les flippers doivent pouvoir être utilisés à tout moment par le joueur et cela sans latence. Pour pallier à ce problème j’ai décidé d’utiliser la fonction millis() qui renvoie le temps écoulé en millisecondes depuis le début du programme. Ainsi j’enregistre dans une variable ce temps à chaque fois qu’un passage est détecté et je peux comparer le temps du dernier passage avec le temps actuel. Avant d’incrémenter le nombre de passages je vérifie que la dernière détection du capteur infrarouge date de plus de 100 millisecondes afin d’éviter qu’une balle ne passant pas assez pas assez rapidement devant le capteur soit comptabilisée plusieurs fois.

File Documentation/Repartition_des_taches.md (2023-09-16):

Programme des 8 séances hebdomadaires dédiées au projet :
Ce programme est susceptible de varier légèrement en fonction du délai de livraison des pièces commandées et des difficultés rencontrées.

**Séance 1:**
Choix d’une planche à découper aux dimensions voulues. 
* Adrien : Création des contours du Flipper, test de positionnement d'un prototype de flipper pour y installer les moteurs lors de la séance suivante. Prise en main des capteurs infrarouges.
* Redha : Esquisse du Flipper sur une planche au crayon, positionnement de la zone de lancement et conception du lanceur.

**Séance 2:**
* Adrien : Installation des flippers avec moteurs (+ code) puis installation de quelques capteurs infrarouges.
* Redha : Création des slingshots + test de fonctionnement.

**Séance 3:**
* Adrien : Installation des bumpers.
* Redha :  Poursuite de l'installation des slingshots + installation du servomoteur ramenant la bille dans la zone de lancement.

**Séance 4:**
* Adrien : Création des cibles et ajout de points.
* Redha : Suite du fonctionnement des bumpers.

**Séance 5:**
* Adrien : Configuration et installation de l'écran LCD pour afficher le score du joueur.
* Redha :  Installation des LEDs en déterminant quelles LEDs allumer en fonction des capteurs déclenchés.

**Séance 6:**
* Adrien : Installation d'une pièce avec un servomoteur permettant de relâcher d'autres billes depuis le haut du flipper lorsque le mode Multibille est déclenché.
* Redha : Création et installation de rampes.

**Séance 7:**
* Adrien :  Création de la roue de la fortune, déclenchée par exemple si les 3 cibles sont touchées, permettant de remporter des bonus ou de mettre en marche le mode multiball. Cette étape sera réalisée seulement s'il reste du temps (donc à condition que tous les composants conçus et installés lors des séances précédentes fonctionnent correctement).
* Redha : Début de décoration, débogage du code.

**Séance 8:**

Débogage, finitions et décorations.

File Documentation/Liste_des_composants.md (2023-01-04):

Les liens des composants à acheter: 

5 billes métalliques de 16 mm de diamètre(il faut choisir l’option 16mm 5PCS): 
https://fr.aliexpress.com/item/1005004860741892.html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

2 Roulement à billes 608zz 8x22x7mm: https://fr.aliexpress.com/item/1005004632265970.html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

Environ 12 capteurs infrarouges

2 solénoïdes 24V et pour flippers (1564B 3.5-65N 20mm) : 
https://fr.aliexpress.com/item/1005004016711403.html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

3 solénoïdes 24V pour bumpers(0630B 0.4-8N 10mm ): 
https://fr.aliexpress.com/item/1005004016711403.html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

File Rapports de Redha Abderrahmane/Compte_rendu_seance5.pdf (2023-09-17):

Compte-rendu séance 5

Objectif de la séance : Commencer à travailler sur la planche finale du projet.

Avant de commencer nous devons d’abord choisir l’emplacement des Bumpers, capteurs infrarouges, Flippers et Slingshots sur la planche.


Comme vous pouvez le voir sur l'image, les Bumpers seront placés en forme de triangle équilatéral, séparés par une distance de 100mm. Les pièces de couleur noire serviront de voies possibles pour la bille lorsqu'elle sortira de la zone de lancement et sera guidée par la bordure de la planche. Dans chacune des trois voies, un capteur infrarouge sera installé pour détecter le passage de la bille, ce qui permettra d'incrémenter le score du joueur.

De plus, nous avons testé le fonctionnement des Bumpers avec le système de détection de bille constitué d'un anneau et de la plaque métallique.

Rappel du fonctionnement : lorsque la bille métallique entre en contact direct avec l'anneau (connecté au 5V) et la plaque métallique (connectée à la broche digitale de l'Arduino), le circuit se ferme et le solénoïde se déclenche.


Test des Bumpers avec le système de détection

Pendant la séance, nous avons décidé de graver l'emplacement des plaques métalliques sur la planche (pour les Bumpers) et de percer les trous (pour les capteurs infrarouges). Le tout sur une planche de dimensions 290x600 mm et d'épaisseur 3 mm. L'objectif est de réaliser les découpes et les gravures sur des planches séparées, puis de les coller sur une grande planche de support de dimensions 414 mm x 800 mm.

À l'aide du logiciel Inkscape, j'ai créé le fichier permettant à la machine d'effectuer avec précision les découpes et les gravures sur la planche.


Image de l’emplacement des trous à percer (en rouge) et des zones à graver (en noir).

Les cercles rouges définissent les zones à percer. Les carrés noirs, les zones de gravure pour les plaques métalliques, et les rectangles noirs, les zones de gravure pour les capteurs infrarouges.

En ce qui concerne la gravure pour les capteurs infrarouges, celle ci permettra de poser du plexiglas au-dessus des capteurs pour maintenir le même niveau sur la planche et donc éviter que la bille ne reste bloquée dans l'un des trous. Mais aussi pour protéger le capteur en cas de contact à grande vitesse.

Pendant la séance, nous avons reçu les relais ainsi que le reste des solénoïdes. Nous allons donc pouvoir commencer à installer les composants sur la planche principale et débuter le câblage lors de la prochaine séance.

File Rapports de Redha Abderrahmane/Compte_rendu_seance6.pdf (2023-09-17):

Compte-rendu séance 6

Objectif de la séance: Terminer le travail sur les planches.

Pendant cette séance, nous avons continué à travailler sur les planches que nous allons coller pour commencer à installer les composants.

Cette étape est importante et demande de la précision afin de ne pas perdre de temps pendant la séance, mais aussi afin d'éviter de gaspiller des planches de bois en cas d'erreur.

1) Planche supérieure du flipper:

Voici le résultat de la première planche mentionnée dans le rapport de séance n°5:


Photo d'une des planches avec l'emplacement des bumpers et des capteurs infrarouges.

Comme vous pouvez le voir sur la photo, nous avons vérifié l'emplacement des plaques métalliques sur la planche et nous nous sommes assurés que la bille puisse rouler facilement sur la surface métallique. Une plaque de plexiglass sera installée dans le trou rectangulaire de la planche. Nous avons également ajouté deux trous de 22 mm de diamètre sur cette planche pour l'emplacement des capteurs infrarouges.

Ceux-ci permettront de détecter si la bille est entrée dans une rampe (les trous ne sont pas visibles sur la photo ci-dessus car ils ont été réalisés à la fin de la séance). En effet, nous allons installer lors des prochaines séances deux rampes qui commencent sur cette planche et s'étendent jusqu'à la partie inférieure du flipper.

2)Planche inférieure du flipper:

Pour la partie inférieure du Flipper, nous avons commencé par déterminer l’emplacement définitif des slingshots, des flippers, et des capteurs infrarouges.


Modélisation 3D de la partie inférieure du Flipper (par Adrien Waeles-Devaux)

Pour cela, nous avons créé un fichier SVG pour découper la planche inférieure.


Emplacement des trous à découper sur la planche inférieure

Les cercles de diamètre 22 mm sont destinés à l'emplacement des capteurs infrarouges. Les cercles de diamètre 3 mm sont destinés à l'emplacement des flippers et des slingshots, tandis que les trous rectangulaires de 28 x 15 mm permettent l'installation du levier qui pousse la bille lors du contact avec l'élastique des slingshots. Le trou rectangulaire présent sur la partie inférieure de la planche permet l'installation d'un bras mécanique qui pousse les billes vers la zone de lancement en fin de la partie.

3)Planche du centre du jeu:

Nous avons choisi le thème de Game of Thrones pour décorer notre flipper.

Dans cette optique, nous avons décidé de graver quelques personnages emblématiques de la série ainsi que la célèbre phrase 'Winter is coming' sur la planche centrale du flipper.


Planche gravée au laser avec les personnages de Game of Thrones

Nous avons également l'intention d'ajouter des logos et des références imprimés en 3D de la série sur les éléments du jeu.

4) Bordures du Flipper:

À partir des bordures de la maquette 3D transformées en fichiers SVG, nous allons découper à la graveuse laser quatre planches de 5 mm d'épaisseur, afin d'obtenir des bordures de 20 mm d'épaisseur au final. (La découpeuse laser n'étant pas assez puissante pour découper directement du matériau de 20 mm d'épaisseur).

Sur Inkscape, j'ai regroupé les pièces à découper dans le même fichier et j'ai modifié leurs dimensions pour qu'elles correspondent à la taille de notre planche.


Fichier SVG contenant les bordures à découper

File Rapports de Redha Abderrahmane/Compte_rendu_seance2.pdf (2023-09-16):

Compte rendu séance 2

Le but de cette séance est de construire un prototype pour les slingshots et les cibles.

1) Slingshot:


Le slingshot est construit avec trois composants : trois vis, des élastiques permettant le rebond de la balle, et un solénoïde pour amplifier le rebond de la balle sur l'élastique.

Pour détecter le contact de la balle avec l'élastique, nous utilisons un microswitch placé à quelques millimètres de celui-ci. Une fois enfoncé, il déclenche le solénoïde qui est connecté à un petit bras en plastique permettant de pousser l'élastique.

Démonstration du slingshot: https://www.youtube.com/watch?v=Ld9HjYVpliU&ab_channel=AdrienWaeles-Devaux

Comme vous pouvez le constater, le rebond de la balle est suffisamment puissant pour lui permettre de retourner dans la zone de jeu. On peut obtenir plus de puissance en connectant un mécanisme de levier au solénoïde plutôt que de dépendre uniquement de la puissance du solénoïde.

La taille du slingshot doit d'ailleurs être ajustée en fonction des dimensions de la planche finale : deux planches de 30 cm x 60 cm, dans la mesure du possible

2) Cibles:

Au cours de cette séance, j'ai soudé les câbles aux pattes des trois microswitches qui représentent les cibles. Nous avons également testé le prototype de la boîte qui contiendra les microswitches et dissimulera leur câblage.


Modélisation 3D de la boîte des cibles

La boîte sera fixée sur la planche à l'aide de deux vis, et il faudra ajouter trois trous en dessous de chaque cible pour faire passer les câbles sous la planche. De plus, une LED sera positionée au-dessus de chaque cible.


Photo des cibles avec les microswitches installés dans la boîte

Comme vous pouvez le constater, les microswitches ne sont pas entièrement installés dans la boîte. Nous devons ajuster les dimensions des emplacements ainsi que leur profondeur pour permettre une installation complète de ceux-ci.
J'ai également acquis de l'expérience dans les étapes de soudure de fils, et rencontré des difficultés, notamment liées à l'utilisation de fils non adaptés au soudage.
3) Discussion par rapport au lanceur de bille:


Image de lanceur de bille (trouvée sur Youtube, credit: Adam pinball)

Dans notre projet, la tige sera en bois, et la poignée a déjà été modélisée en 3D par Adrien Waeles-Devaux. La bille métallique qui sera utilisée pour jouer mesure 16 mm de diamètre.

Nous avons effectué quelques recherches concernant les ressorts capables de propulser une bille à grande vitesse. Cependant, le poids de la bille métallique utilisée pour le projet n'est pas connu.

Théoriquement, ma mission pour la prochaine séance consiste à installer les microswitches et les LEDs dans la boîte, à assembler le lanceur de bille (nous le testerons avec plusieurs ressorts pour obtenir la meilleure force de rappel avec la bille métallique), et à commencer à travailler sur les bumpers (et sur les slingshots si nécessaire).

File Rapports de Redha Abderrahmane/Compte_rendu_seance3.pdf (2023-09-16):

Séance 3 : Projet Flipper Arduino

1- Bumpers:
Le but de cette séance est d'entamer nos recherches sur les bumpers et de concevoir le lanceur de bille.

Définition d'un bumper : élément de jeu en forme de champignon disposé sur le plateau de jeu, dont la fonction est de repousser la bille.


Photo de bumpers
Lorsque la balle roule sur la surface jaune en plastique, le solénoïde se déclenche pour pousser la pièce en forme de champignon vers le bas.

Démonstration du fonctionnement d’un bumper:
Mécanisme:
https://youtube.com/shorts/08TMJ_lJdZU?feature=share

Exemple:
https://www.youtube.com/watch?v=kxyMmFz1iDg&ab_channel=SnyderColorcast

Pour simplifier le fonctionnement des bumpers, nous savons qu'un flipper utilise une bille métallique pour jouer. Ainsi, nous allons exploiter la conductivité de la bille pour faire fonctionner le bumper. En effet, en utilisant un anneau métallique collé sur la pièce en forme de champignon et une surface métallique en dessous du bumper, nous pouvons créer un circuit fermé uniquement lorsque la bille métallique entre en contact à la fois avec l'anneau métallique (connecté au 5V de l'Arduino) et la surface métallique (connectée à l'une des broches digitales).


Exemple:

(Crédit : element14 presents sur Youtube)

Pendant nos recherches, nous avons également trouvé les composants modélisés en 3D qui nous aident à faire fonctionner les bumpers, tels que :


La pièce initiale prend la forme d'un "champignon", qui constitue l'aspect visuel emblématique des bumpers dans un flipper classique. Cette modélisation simplifie le design pour faciliter l'installation.
(Pièce 1)

Cette pièce sert à stabiliser la pièce 1. Elle repose sur un système de rails pour faire coulisser la pièce 1 lorsque le solénoïde est déclenché (i.e lorsque la balle touche le bumper).


Source:https://www.thingiverse.com/thing:3286052/files

Pour notre projet, nous envisageons d'utiliser ces pièces, mais avec une modification des dimensions, et nous remplaçons la surface métallique par du ruban de cuivre, car il s'agit d'un conducteur que nous pouvons facilement coller sur la planche de jeu.

Les solénoïdes qui seront utilisés sont du modèle : 0630B 0.4-8N avec une course de 10mm. Nous devons également créer un support pour installer les solénoïdes verticalement en dessous de la planche.

Dimensions du solénoïde que le support doit respecter :

- Dimensions de la totalité du solénoïde:

longueur=29.2mm
largeur=18.96mm
- Dimensions des trous dans le solénoïde : diamètre : 3mm.

diamètre=6.91mm du côté rond diamètre=6.31mm du côté plat

- Dimensions du cylindre du solénoïde:

2- Lanceur de bille:

Durant cette séance, l'objectif était également d'assembler le lanceur de bille à l'aide d'une poignée modélisée en 3D et d'une tige en bois. Cependant, le plan a été modifié lorsque l'un des enseignants nous a conseillé d'imprimer l'ensemble de la pièce en 3D pour éviter qu'elle ne se fragilise lors d'une utilisation répétée du lanceur de bille.

La modélisation 3D du lanceur de bille se trouve dans le compte rendu d'Adrien Waeles-Devaux.

Difficultés rencontrées pendant la séance :
Nous avons fait face à un problème d'alimentation lorsque nous devions déclencher les nouveaux solénoïdes (modèle 0630B 0.4-8N 10mm) que nous avions reçus pour les bumpers. Lorsque nous avons essayé de déclencher l'un de ces solénoïdes, nous avons remarqué qu'il y avait un faux contact au niveau de la connexion de la nouvelle alimentation (dont la tension est désormais de 24V). Par conséquent, nous devons veiller à bien vérifier les connexions électriques tout au long du projet afin d'éviter de perdre du temps à diagnostiquer un problème simple comme celui-ci.

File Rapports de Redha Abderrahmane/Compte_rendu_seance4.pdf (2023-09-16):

Compte rendu séance 4 Arduino
1) Bumpers:
Avant le début de la séance, nous avons adapté les dimensions des pièces utilisées pour les bumpers et les avons imprimées. Nous avons également imprimé un support pour fixer le solénoïde en dessous de la planche. Pendant la séance, nous avons testé le bon fonctionnement du mécanisme ainsi que l'activation du solénoïde (modèle 0630B 0.4-8N 10 mm) alimenté en 24V.

En ce qui concerne le déclenchement des bumpers, j'envisage de placer un anneau métallique sur la partie supérieure du bumper. Nous avons également discuté avec l'un des professeurs qui nous a suggéré de remplacer le ruban de cuivre par une plaque métallique, comme indiqué dans la photo ci-dessous en exemple :

Exemple de cette méthode (crédit : element14 presents)


La méthode proposée par le professeur consiste à créer un trou à l'aide d'une graveuse laser de manière à ce que la plaque métallique soit à ras de la planche et n'influence pas la trajectoire de la bille. Nous avons réalisé un premier prototype des bumpers avec la plaque métallique placée sur la planche.

Comme vous pouvez le constater, il nous manque encore l'anneau métallique à fabriquer. Nous envisageons d'ajouter un passage pour le câble de l'anneau métallique dans la pièce supérieure des bumpers et d'ajuster la hauteur de cette pièce afin d'obtenir plus de puissance lorsque la balle entre en contact avec les bumpers.


Photo d’un bumper avec une plaque métallique

J'ai testé le fonctionnement du dispositif détecteur de contact avec deux morceaux de feuille d'aluminium en utilisant le code suivant :


2) Cibles:
Lors des séances précédentes, nous avons fabriqué la cage imprimée en 3D pour les cibles. Durant cette séance, j'ai soudé les fils et les résistances sur les leds. J'ai remarqué que les microswitches ne peuvent pas être installés correctement lorsque les leds et leurs fils sont dans la cage, donc nous devons modifier la profondeur de la cage pour avoir suffisamment d'espace pour les leds et les microswitches.

Exemple de la position du microswitch lorsque la led est installée.


J'ai retravaillé le code de test des microswitches pour éviter l'enregistrement de plusieurs entrées lorsque le bouton est appuyé seulement une fois en raison du phénomène de rebond d'un interrupteur. Et cela en utilisant la bibliothèque ezButton.


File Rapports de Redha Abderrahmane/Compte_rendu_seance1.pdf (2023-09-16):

ABDERRAHMANE REDHA G2
Compte rendu séance 1;

Contexte:

Le but de cette séance était de sélectionner la planche de jeu pour le Pinball, d'esquisser l’emplacement des composants sur celle-ci, ainsi que de tester notre prototype de flippers

### imprimés en 3D. En raison de l'absence de la planche lors de la première séance, nous avons décidé de nous concentrer sur la partie électronique et le mouvement des flippers

avec la prise en main de solénoïdes.

Solénoïdes: un dispositif constitué d'un fil électrique en métal enroulé régulièrement en hélice de façon à former une bobine
générant un champ magnétique lorsque du courant y passe.


Des solénoïdes

Microswitch (micro-interrupteur): Un interrupteur miniature à action instantanée est un interrupteur électrique qui est actionné par très peu de force physique.

Un micro switch

Première partie:

Avant la séance, nous avons modélisé et imprimé un prototype des flippers pour ensuite
tester le fonctionnement de ce mécanisme.


La tige des flippers sera emboîtée dans la deuxième partie en dessous de la planche. Cette
dernière sera connectée à un solénoïde qui permettra de la mettre en mouvement.
Dans un premier temps, nous avons testé en groupe le fonctionnement d'un solénoïde à l’aide d’un transistor qui permet d’alimenter le solénoïde par une alimentation de 12V. Le solénoïde est ensuite contrôlé par la carte Arduino.
Suite à cette expérience, nous risquons de changer le solénoïde de 12V pour un solénoïde fonctionnant en 24V afin d'avoir assez de puissance pour envoyer la bille vers les cibles (qui sont très éloignées des flippers).
Ce qui implique aussi de choisir une alimentation adaptée.

Démonstration :
https://www.youtube.com/watch?v=6iraHV_b1UE&ab_channel=AdrienWaeles-Devaux Remarque : La partie code a été faite par Adrien Waeles.

Deuxième partie:

Je me suis familiarisé avec les micro switches inverseurs 10T85 par la mise en place d’un

### montage simple et d'un code pour tester leur fonctionnement :


Le but est d’utiliser ces microswitches comme des cibles où le joueur peut gagner des points si la balle les touche. Le score sera affiché à l'aide d’un écran LCD.

### Pour la prochaine séance, nous envisageons de souder des câbles électriques aux trois

points de connexion des microswitches pour éviter les faux contacts et simplifier le câblage des cibles.

### Un code simple pour la démonstration (avec 1 microswitch) :


### Inspiration retenue pour la réalisation des cibles en fin de projet :

Les parties en bois peuvent être remplacées par des pièces imprimées en 3D


Source: Wooden Pinball + Arduino DIY (40x40cm mini size)(Youtube)

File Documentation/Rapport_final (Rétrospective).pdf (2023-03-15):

## Projet Flipper avec Arduino


Par Adrien Waeles-Devaux et Redha Abderrahmane

Sommaire :
1) Présentation du projet
2) Objectif
3) Planning et déroulement
4) Présentation des différents éléments de notre flipper.
5) Maquette du projet
6) Schéma électrique
7) Algorithme
8) Difficultés rencontrées
9) Coût du projet
10) Perspectives futures
11) Conclusion
12) Bibliographie
1) Présentation du projet

Dans le cadre des cours d'Arduino de 2ème année de classe préparatoire intégrée à Polytech Nice-Sophia, nous avons choisi pour projet la conception d’un flipper à partir de composants simples. Le principal atout de ce projet étant sa pluridisciplinarité nous permettant de nous auto-former dans des domaines nous passionnant tels que la mécanique, l’électronique et la programmation.

2) Objectif :

Depuis l'apparition des jeux vidéos, les flippers deviennent de plus en plus rares et semblent en voie de disparition. Cela peut s'expliquer par un coût de fabrication et de maintenance bien plus élevé qu’un jeu numérique.


Flipper “Bram Stoker’s Dracula” et sa complexité technique (Source : pinballmag.fr)

L'objectif de ce projet était donc de montrer qu'il est possible de créer son propre flipper avec des composants simples en utilisant Arduino face à des machines vendues neuves autour de 10 000 euros.

3) Planning et déroulement:

Ce projet a exigé un grand travail d’organisation et beaucoup d'implication en dehors des cours puisque les 8 séances de 3h dont nous bénéficions étaient loin d’être suffisantes pour accomplir notre vision du projet. Pour compenser ce manque de temps, nous avons travaillé tous les après-midis après les cours et pendant les vacances pour accomplir le niveau d’avancement démontré lors de la présentation. Environ 600 h (en cumulant le travail de chaque membre du binôme) ont été passées sur le projet jusqu’au jour de la soutenance finale.
En estimant le coût de travail sur la base d’un salaire ingénieur de 38 000 euros pour 1600h de travail, cela équivaut à un total de 14 250 euros.
Redha ≈ 250h → 5938 €
Adrien ≈ 350h → 8312€


Le diagramme de Gantt ci-dessus montre l’avancement du projet sur nos 13 semaines de travail. Ainsi on constate que la modélisation 3D a pris un temps considérable puisque nous avons imaginé toutes les pièces de notre flipper. La fabrication et l’assemblage ont également pris une grande partie de notre temps puisque c’était la première fois que nous travaillions sur un projet de cette envergure. Nous avions donc un manque d'expérience dans la fabrication et l’assemblage de pièces techniques.
La prise en main de nouveaux logiciels et de nouveaux outils, a nécessité un temps non négligeable avant d’acquérir un bon niveau de maîtrise pratique et théorique pour avoir le meilleur résultat possible. Ce temps d’apprentissage explique les fluctuations entre notre planning initial disponible sur notre github et ce diagramme. Cela découle également de la durée de livraison des composants qui a nécessité une réorganisation afin de ne pas perdre de temps.
4) Présentation des différents éléments de notre flipper:

La documentation en ligne sur le fonctionnement des flippers est assez riche et très instructive, cependant, la mécanique d'un flipper est si complexe qu'il n'était pas envisageable d'utiliser les mêmes composants et mécanismes pour réaliser un projet abordable et le rendre dans les temps impartis.
Nous avons donc dû concevoir tous nos éléments par nous-mêmes.
Pour cela nous avons choisi de réaliser des prototypes sur des petites planches de bois en premier lieu afin de pouvoir effectuer de nombreux tests avant la version finale. Au total plus de 25 pièces ont été modélisées en 3D ayant chacune nécessité de nombreuses modifications et essais.

Voici les différents éléments que nous avons créé :

Les flippers :
Pièces portant le nom du jeu contrôlées par le joueur et permettant de frapper la bille pour l'envoyer dans les différentes zones de jeu.


Ceux-ci sont activés par 2 puissants électro-aimants à l’aide d’un mécanisme modélisé et imprimé en 3d permettant de transformer le mouvement linéaire de ceux-ci en un mouvement de rotation.

Les bumpers :


Pièces iconiques en forme de champignons qui vont s'abaisser sur la bille lorsqu'ils sont touchés pour la renvoyer dans la direction opposée. Ils sont souvent disposés en triangle avec un faible écartement afin que la bille puisse faire des allers-retours entre ceux-ci pour cumuler un maximum de points.

Les bumpers sont déclenchés lorsque la bille est en contact à la fois avec un fil de cuivre qui est inséré dans celui-ci et une plaque métallique incrustée dans la planche comme détaillé dans la partie câblage.

Les slingshots :
Pièces munies d'un élastique permettant de renvoyer la bille dans la direction opposée afin de la repositionner dans une zone jouable. Ceux-ci sont déclenchés grâce à 2 micro-interrupteurs placés aux extrémités de chaque élastique qui permettent de détecter l’impact de la bille sur celui-ci.

Les cibles :


Celles-ci fonctionnent également avec des micro-interrupteurs. Lorsque la bille va venir frapper une cible, elle va enclencher son interrupteur. Le signal reçu par l’arduino va permettre de comptabiliser les points.

La roue de la fortune :

Élément unique à notre flipper. Lorsqu'elle est déclenchée (après que le joueur ait visé toutes les cibles par exemple), celle-ci va permettre de remporter un bonus choisi aléatoirement. Elle fonctionne avec une animation lumineuse de néo-pixels qui s’allument successivement selon un motif circulaire, l’animation termine avec le clignotement d’un néo pixel indiquant le bonus remporté sur la roue.


La poignée de lancement :


La poignée est entièrement imprimée en 3D. Afin de pouvoir insérer l’insérer dans un support dans lequel elle va coulisser et d'y insérer un ressort, celle-ci a été modélisée en 3 parties. Cela permet également de limiter l’ajout de supports lors de l’impression 3D. Les 3 parties s’assemblent grâce à un filetage réalisé sur Fusion 360. La photo ci contre montre l’assemblage des 3 pièces imprimées en 3d sur lesquelles on a inséré un ressort permettant de propulser la bille.

Zone de lancement :
Lorsqu'une bille n’est pas réceptionnée par le joueur, il faut pouvoir être capable de la ramener dans la zone de lancement afin que le joueur puisse avoir un nouvel essai. Pour cela nous avons conçu une petite pièce plastique fixée sur un solénoïde qui, lorsque celui-ci est enclenché, va pousser la bille pour l’envoyer juste au-dessus de la poignée.

La rampe :
L’entrée de notre rampe est entièrement modélisée et imprimée en 3d, pour la suite de la rampe nous avons soudé plusieurs fils de cuivres rigides entre eux en veillant à garder un écartement constant tout au long de la rampe pour que la bille de tombe pas.
5) Maquette du projet :


Avant l'assemblage, nous avons décidé de réaliser une maquette complète du projet en important et disposant tous les éléments modélisés lors de la phase de conception afin d'éviter de nombreuses erreurs de placement.

Celle-ci a été très utile puisqu’elle a permis de découper nos planches en ajoutant les trous de fixation et de placement de nos différents composants afin de gagner un temps considérable. Elle a également servi de support pour la conception des bordures du flipper faites sur le même logiciel puis transformées en fichiers 2d vectoriels afin de pouvoir les découper au laser.

6) Schéma électrique:


Schéma du câblage du projet sur le logiciel fritzing

Tout d’abord voici quelques notions à connaître afin de mieux comprendre les détails du câblage:

- Les solénoïdes sont des électroaimants qui permettent de transformer de l'électricité en mouvement mécanique en générant un champ magnétique. À l’intérieur, un fil est enroulé sous forme de bobine. Quand le courant passe dans un fil, il génère un champ magnétique. Celui-ci va alors déplacer le piston métallique vers l’intérieur. Lorsque le courant est coupé, le ressort du solénoïde permet au piston de revenir dans sa position initiale.
- Les relais sont des composants qui permettent de contrôler
des charges électriques externes à partir de signaux
numériques. Lorsque le signal est appliqué, le relais commute un contact à l’aide d’un électroaimant afin d’ouvrir ou fermer un circuit électrique.
Dans notre cas les relais sont utilisés pour isoler le circuit de commande de la charge électrique (qui est géré par l’arduino fonctionnant à des tensions proches de 5V) de
l’alimentation des solénoïdes qui fonctionne en 24V.
Ceux-ci sont munis d’une diode qui permet d’éviter que les


charges emmagasiné soient renvoyées dans l’autre sens vers l’arduino quand le courant est coupé.

Dans notre projet, nous avions besoin de solénoïdes capables d’envoyer la bille avec une grande vitesse et réactivité vers toutes les zones jouables de notre flipper. Pour cela nous avons choisi d’utiliser des solénoïdes capables d’une force de 65N fonctionnant en 24V.
Cette restriction nous a forcé à alimenter notre projet à l’aide d’une boîte d’alimentation capable de fournir une tension de 24V et 2A de courant.

Les solénoïdes sont connectés en parallèle pour pouvoir les activer individuellement ou simultanément et leurs masses sont toutes reliées à une masse commune.

Les deux solénoïdes des flippers sont contrôlés directement par le joueur grâce aux boutons poussoirs fixés sur les bordures de la planche. Pour cela, ces interrupteurs sont reliés directement aux relais afin d’activer les solénoïdes directement lorsque le circuit est fermé.

Pour alimenter le cerveau qui contrôle notre projet c'est-à-dire la carte Arduino Mega, nous avons utilisé un convertisseur de tension progressif permettant de recevoir 24V en entrée afin d’avoir en sortie 5V.

De même cela nous a permis d’alimenter les composants suivants qui fonctionnent avec de faibles tensions :
- | Micro-interrupteurs | - Ecran LCD | -Buzzer
- | Capteurs Infra-rouges | - Néo-pixels

Le schéma étant très chargé nous n’avons pas représenté le branchement des plaques métalliques et anneaux des bumpers.
Le fonctionnement est simple, les anneaux métalliques sont connectés au 5V alors que les plaques métalliques sont reliées à la masse commune. Ainsi, la bille étant métallique, lorsqu’elle est en contact à la fois avec l’anneau et la plaque alors le circuit devient fermé et le bumper s’active.
7) Algorithme:

Bien que relativement simple, l'algorithme est assez long à détailler. Nos explications portent donc uniquement sur les points les plus importants et le code commenté sera disponible sur le github. Détaillons le fonctionnement de la zone de lancement :


| | | L’objectif est de ramener la bille au-dessus de
| | | la poignée de lancement lorsqu’elle est perdue
| | | par le joueur.
| | | Pour cela un capteur infrarouge détecte le
| | | moment de sortie de jeu de la bille. On va
| | | alors attendre un instant pour que la bille se
| | | place devant le solénoïde. Il suffira ensuite de
| | | l’activer pour pousser la bille selon un chemin
| | | délimité par nos bordures jusqu’à sa position
| | | de lancement.
| | | Notre difficulté était d’éviter toute interruption
| | | entre 2 commandes afin de ne pas suspendre
| | | tout le programme.

Voici le fonctionnement : si la bille passe sur le capteur IR, alors on enregistre l’instant de détection en secondes et une variable d’état bille détectée prend la valeur “vrai”. Le programme teste en continu si le temps écoulé depuis cette détection solénoïde est supérieur à 1,5 secondes et si bille détectée est égale à vrai. Si c’est le cas, on déclenche le solénoïde. Enfin la variable bille détectée reprend la valeur “faux” afin que le l’algorithme puisse à nouveau être exécuté.

Le fonctionnement des bumpers est bien plus simple :
La broche de l’arduino reliée à l’anneau du bumper est définie en INPUT_PULLUP afin de pouvoir utiliser la résistance de rappel intégrée à l’Arduino.
On cherche alors à savoir si le circuit anneau/plaque métallique est fermé. Pour cela il suffit de tester en continu si l’anneau a une tension nulle (donc si il est relié à la masse). Si c’est le cas, on active le solénoïde et on incrémente le score.
Pour activer le solénoïde pendant 100 millisecondes on peut simplement utiliser un délai car celui-ci est tellement court que la bille n’aura pas le temps de déclencher un autre élément pendant ce temps. En effet, les flippers ne sont pas contrôlés par l’Arduino comme expliqué dans la partie câblage, donc cela ne perturbe pas le jeu.


8) Difficultés rencontrées:
Ayant dû affronter toutes les étapes de réalisation d’un projet, de la conception jusqu'à l’assemblage nous avons rencontré plusieurs difficultés :


-Tout d’abord notre premier prototype de slingshot ne permettait pas de renvoyer la bille assez fort avec le matériel que nous avions. Celui-ci était réalisé à partir de 3 vis tendant un élastique et un petit bras imprimé en 3D poussant celui-ci. (voir première photo ci dessus)
Pour pallier cela, nous avons donc conçu un nouveau système qui repose sur l’utilisation d’un levier. En effet, ce système permet de gagner en amplitude de mouvement et en force.

Pour cela, nous avons modélisé une première pièce en 3D sur laquelle nous avons testé différents points de pivots et longueur. Puis nous avons testé ce prototype sur une planche et modifié la pièce en tenant compte de ces résultats afin de réaliser la version finale et de l’imprimer (voir photo ci-dessus à droite).

- La bille n’était pas réceptionnée dans la zone de lancement car le solénoïde l'envoyait avec une trop grande vitesse. La solution était de régler le temps d’activation du solénoïde via le programme de l’Arduino, ce qui va envoyer la bille avec plus ou moins de force.

-Les bumpers n’étaient pas assez sensibles. En effet la bille ne faisait pas toujours contact entre l’anneau et la plaque métallique. Nous avons donc ajusté leurs hauteurs afin que la bille puisse toucher le fond du bumper.

-Finalement l’inconvénient d’avoir utilisé des capteurs infrarouges dans notre projet, est qu’ils dépendent de l'éclairage de la pièce. Dans une démarche d’amélioration du projet nous aimerions les remplacer par un autre modèle de capteur plus fiable.

9) Coût du projet

Estimation du coût du projet en matériel (en se basant sur les tarifs d’Amazon) : Composants électroniques :
- Carte arduino mega = 25€
- 2 solénoïdes 24V 65 Newtons = 60€
- 6 solénoïdes 24V 8 Newtons = 60€
- Convertisseur progressif = 8€
- 8 relais = 14€
- 8 capteurs infrarouges = 10€


Pièces diverses :
- 3 billes de 16 mm = 5€
- Larges élastiques caoutchouc : 2€
- Visserie ≈ 15€

Coût total : environ 265€

10) Perspectives futures

Ce projet a dû être entièrement réalisé en 13 semaines afin de le rendre dans les délais impartis, cela nous a obligé à nous concentrer sur l’essentiel afin d’être sûr de pouvoir présenter une première version finalisée à temps. Cependant les perspectives d’évolution sont nombreuses. Ainsi nous aimerions rajouter des ruban néopixels pour créer une décoration lumineuse intéractive qui change de couleur ou clignote en fonction des éléments de jeux touchés ou encore ajouter de nouveaux éléments visables par le joueur.
Nous avons commencé à concevoir un mode multibille grâce à une pièce imprimée en 3D et un moteur pas à pas relâchant plusieurs billes au même moment.
Finalement, nous souhaitons continuer la décoration et thématisation du flipper grâce à l'impression 3D, la gravure laser et la conception d’autocollants.

11) Conclusion :

Ce projet nous a passionné, la complexité de sa mécanique de fonctionnement ainsi que la richesse des composants électroniques a été très formatrice. Nous avons développé de nouvelles méthodes de travail en termes de recherche et développement et gagné en efficacité et autonomie.
Finalement cela a permis de renforcer nos choix d'orientation puisque Redha Abderrahmane souhaite s'orienter en spécialité Électronique et Adrien Waeles-Devaux en Robotique

Afin de contribuer à rendre la fabrication d'un flipper plus accessible, toute la documentation, les modélisations et autres fichiers de fabrication sont disponibles en open source sur ce github.

12) Bibliographie :
Documentation :
Flipper, Wikipedia
wikipedia.org/wiki/Flipper (https://fr.wikipedia.org/wiki/Flipper)
Pinball Makers (Ressources pour construire son propre flipper)
pinballmakers.com

Vidéos :
“How a Pinball Machine works in Slow Motion - The Slow Mo Guys” : youtu.be/Tmg5WOvPKpU "Wooden Pinball + Arduino DIY”: youtu.be/y2FeiB1704w
"Fabriquer un FLIPPER, un ENFER", youtu.be/RLwirZu9_jc
Inspiration pour le fonctionnement des bumpers: youtu.be/yfZipK-Nqeo
“DIY 3D printed pinball machine”: youtu.be/SnD3WfmEfXY

Fichiers 3D utilisés:
Bumper | complètement | modifié | pour | le | faire | correspondre | à | notre | projet:
www.thingiverse.com/thing:3286052
Cales pour aligner les flippers avec la bonne inclinaison:
www.thingiverse.com/thing:1644154

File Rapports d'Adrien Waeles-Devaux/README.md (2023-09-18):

Ce répertoire contient tous les comptes-rendus de fin de séance réalisés par Adrien Waeles-Devaux. 

Le calendrier de réalisation du projet était en effet structuré par 8 séances de cours en autonomie (de 4h chacune) avec la possibilité de continuer à travailler sur le projet entre les différentes séances.

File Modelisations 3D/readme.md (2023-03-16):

Vous trouverez ici, toutes nos modélisations des pièces imprimées en 3d du pinball.

Les pièces des bumpers ont été créés par "fluxwood" et sont disponibles à cette adresse : https://www.thingiverse.com/thing:32860, nous avons modifié les dimensions de ces pièces pour les adapter à nos solénoides et à l'épaisseur de notre planche tout en rajoutant une encoche permettant d'y insérer un fil de cuivre.

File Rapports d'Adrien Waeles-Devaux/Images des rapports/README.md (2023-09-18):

Ce dossier contient toutes les images importées dans les rapports de séances

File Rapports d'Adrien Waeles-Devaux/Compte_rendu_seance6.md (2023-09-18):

**Avant la séance :**

Nous avons finalisé la réalisation d’un fichier vectoriel en svg sur Inkscape délimitant nos gravures et découpes pour la partie haute du flipper afin d'utiliser une découpeuse laser.

Ces trous permettent notamment de fixer nos bumpers et les gravures en forme de carrés de positionner 3 plaques métalliques à ras de la surface de la planche pour détecter si la bille roule en dessous d’un bumper. 
Le grand trou rectangulaire permet de positionner une plaque de plexiglass sous laquelle se trouvera un capteur infrarouge permettant de détecter un passage de bille.



Pour rappel, étant donné que notre planche de jeu de dimensions 414 x 800 x 5mm est trop grande pour rentrer dans la graveuse laser directement, nous avions décidé d’y coller dessus 3 petites planches de 3mm afin de pouvoir graver celles- ci. 
Redha s’est occupé de la réalisation des fichiers svg de la partie haute et basse du flipper et je me suis occupé du positionnement des éléments à partir de la maquette virtuelle de notre flipper. 

J’ai ensuite créé un fichier vectoriel pour graver un dessin au milieu du flipper en assemblant des images trouvées en ligne. Pour cela j’ai converti des images en svg puis je les ai importées dans inkscape en les positionnant et en les redimensionnant en fonction de la taille totale de la planche du milieu.



Nous avons décidé de thématiser votre flipper avec pour thème la série Game of Thrones et nous étions donc obligés d’anticiper la décoration par la gravure de cette planche car une fois collée sur la planche épaisse il sera impossible d’effectuer de nouvelles gravures.

Et voici le résultat final de la gravure de la partie haute du flipper avec le positionnement d’une des plaques métalliques : 



J’ai également déterminé la position exacte de tous les éléments en bas du flipper sur notre maquette 3D. 

J’ai ainsi dû adapter le modèle précédent du levier du slingshot (pièce dotée d’un élastique renvoyant la bille en zone de jeu) puisque j'ai constaté que le système de levier prenait trop de place, empêchant l'installation des rangées à gauche et à droite des slingshots. J’ai donc réduit l’épaisseur d’une partie du levier en m’assurant que le levier exerce toujours autant de force sur l’élastique et tout en conservant une pièce rigide. Voici la comparaison entre l’ancienne et la nouvelle modélisation :



Et j’ai également dû modifier la modélisation de la pièce tendant l'élastique du slingshot pour l’agrandir afin d'être sûr que le levier puisse effectuer sa course entièrement sans que l'élastique empêche celui ci de revenir en position initiale, la course du levier est ainsi comprise entre l'avant et l'arrière de l'élastique du slingshot. 



Voici la pièce finale imprimée en 3D :



Finalement j’ai placé le trou dans lequel le levier va effectuer sa course à travers la planche sur la maquette 3D du flipper.



J’ai également modélisé et imprimé les délimiteurs de rangées : 



**Pendant la séance :**

Certaines parties du contour étant arrondies, il aurait été difficile de les réaliser directement à la main avec précision. Nous avons décidé de réaliser ces parties du contour par découpe laser. Pour cela j’ai utilisé les pièces modélisées sur la maquette 3D, je les ai séparées de la maquette et je les ai exportées en STL. Voici les pièces en question modélisées sur Sketchup.



Ensuite je les ai importées dans Blender pour les transformer en fichiers 2D vectoriels. Pour cela j’ai utilisé l’extension “outline_to_svg” qui permet de faire un rendu 2D d’une pièce en 3D en positionnant une caméra de rendu dans la vue voulue. Il fallait également simplifier la géométrie des différents arrondis pour que le résultat soit exploitable. Et voici le résultat :



Etant donné que la graveuse laser du fablab est limitée à la découpe de planches de 5 mm maximum. Nous allons découper chaque pièce du contour en 4 exemplaires sur des planches de 5 mm. Puis il faudra coller les 4 morceaux de 5mm les uns sur les autres pour avoir une bordure d’une épaisseur totale de 20mm.

J’ai dessiné l'emplacement des différents capteurs infrarouges, afin d'insérer des plaques de plexiglass à ces emplacements et Redha les a tracés sur Inkscape. (Les emplacements sont désignés par des cercles sur l'image de la maquette en bas du compte rendu).

Il y en a 5 sur la planche, dont 3 qui sont positionnées aux sorties du jeu, et permettent de détecter si le joueur à perdu la bille. En effet on distingue si la bille sort au centre du flipper (le joueur n’a pas réussi à la réceptionner) et les pertes de billes sur les extrémités du flipper qui ne sont pas la faute du joueur. Cela peut permettre par exemple d’offrir un nouvel essai au joueur si une bille est perdue sans l’intervention du joueur quelques secondes après l’avoir lancée. C’est ce que l’on retrouve sur certains vrais flippers avec le message “bille sauvée” et l’ajout d’un nouvel essai. 

Les deux autres trous sont placés sur la partie haute du flipper, ils sont situés à l’entrée des futures rampes que la bille pourra emprunter.

Finalement j’ai ainsi pu avancer la modélisation de la maquette qui a permis de positionner les éléments à découper et graver au laser.
A gauche de la maquette on peut voir l’assemblage des 3 fichiers vectoriels que nous avons réalisés et qui ont permis d’effectuer les gravures et perçages dans nos 3 fines planches.



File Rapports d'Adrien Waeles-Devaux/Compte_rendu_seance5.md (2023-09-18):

**Avant la séance :**

Tout d’abord j’ai pu tester l'écran LCD afin d'afficher des messages et d'actualiser le nombre de points. L'écran est branché à un module I2C ainsi il ne suffit que de 2 câbles de communication branchés aux entrées analogiques de l'arduino en plus de son alimentation: (sur une carte Arduino Uno la broche SDA est connectée au port analogique A4 de la carte et la broche SCL au port A5). Au début l’écran ne semblait pas fonctionner, aucun message ne s'affichait, mais il suffisait de tourner la petite vis au dos pour ajuster le contraste. Voici un programme simple de test :



La fonction afficheScore(int score) permet d’afficher simplement n’importe quel score à l’écran. Elle est appelée dans le void setup avec la valeur 0 car toute partie commence avec 0 points. Pour effectuer des tests j’ai écrit une boucle for dans le void loop qui incrémente un nombre de points de 100 toutes les secondes jusqu'à 10000. Cette fonction pourra être optimisée par la suite.



Pendant les vacances de Noël, j’ai travaillé sur la fabrication des flippers. Pour les modéliser j’ai utilisé les dimensions réelles d’un flipper. J’ai décidé de diviser le mécanisme en 3 pièces : le flipper qui est la pièce frappant la balle muni d'une tige hexagonale qui vient s'emboîter dans la pièce suivante.



La 2ème pièce est un “bras” de flipper, elle est située sous la planche et va permettre de transformer le mouvement de translation du solénoïde en mouvement de rotation. Elle est reliée au solénoide par une 3ème pièce qui tourne autour de son axe.



La 3eme pièce permet de relier le solénoïde au bras du flipper.
Pour cela j'insère cette 3eme pièce dans la 2eme en effectuant une pause dans l'impression 3d pour que cette pièce soit prisonnière dans la 2eme et puisse tourner autour.  Cela permet d’éviter l’ajout de vis supplémentaires. Cette pièce est essentielle car je ne pouvais pas attacher facilement directement le solénoïde qui se déplace linéairement à une pièce qui effectue un mouvement de rotation.



Voici une vue de la planche de dessous de l’ensemble solénoide + attache_bras + bras de flipper : 



J’ai également modélisé une équerre permettant de fixer le solénoïde sous la planche. J'ai rencontré des difficultés pour placer correctement le solénoïde, en effet celui-ci doit être positionné précisément pour que l’axe de la pièce imprimée en 3d ne subisse aucune force supplémentaire, sans cela le solénoïde se bloque et ne revient pas en position initiale grâce à son ressort. Afin de régler le positionnement du solénoïde plus facilement j’ai décidé de remplacer les trous circulaires sur la modélisation de l’équerre pour les remplacer par des rainures. Il suffira alors d’utiliser des rondelles sous les vis pour s’assurer que la pièce soit correctement fixée. J'ai pu alors fixer le solénoïde sur la planche en y perçant un trou et en vissant l'équerre. 



Voici le test du flipper dans une courte vidéo :
https://youtube.com/shorts/JcDkgeMB18o

J’ai ensuite ajouté une encoche circulaire dans la pièce de modélisation du bumper sur Blender qui permet d'y insérer un fil électrique sur lequel la bille va faire contact. J'ai également dû modifier la hauteur de la pièce pour que la bille soit bien en contact avec la planche et le fil du bumper. 



Etant donné que le slingshot (pièce dotée d'un élastique qui va renvoyer la bille dans la zone de jeu en tendant l'élastique) ne renvoyait pas la bille assez fort en raison de la faible course du solénoïde utilisé (10mm) et de sa force peu élevée (8 Newton). 
Suite aux conseils de nos professeurs, j’ai complètement repensé le modèle 3d du slingshot pour y intégrer un système de levier. Celui-ci permet d’avoir une plus grande amplitude de mouvement et une force plus élevée. Pour cela j’ai d’abord réalisé un prototype dans lequel j’ai effectué plusieurs trous pour tester l’emplacement et la longueur optimaux de la barre sur laquelle le levier va effectuer son pivot. 
Voici le résultat après de nombreux essais et modifications de la pièce imprimée :
https://youtube.com/shorts/K7FTkk97wYo

J’ai finalement remodifié la pièce imprimée en tenant des compte des améliorations effectuées pour avoir une pièce propre que je puisse réimprimer également pour le 2ème slingshot. 
Voici l’équerre du solénoide du slingshot modélisée ainsi que le levier :





Etant donné qu’il il a fallu passer un temps énorme sur les prototypes pour placer correctement les composants sur la planche. J’ai décidé de créer une maquette en 3D du pinball sur Sketchup afin d’avoir toutes les mesures nécessaires et gagner en temps et précision sur la version finale. J’ai effectué de nombreuses mesures en me basant sur les différents prototypes réalisés lors des séances précédentes pour déterminer la position exacte de chaque composant. J’ai donc importé toutes les pièces précédemment modélisées afin de les placer. Il reste encore quelques éléments qui seront ajoutés bientôt à la maquette.

 

Finalement j'ai profité de ces vacances pour terminer la modélisation de la poignée sur blender, afin d’avoir une poignée adaptée avec une bonne prise en main.  Cette poignée est liée à une tige autour de laquelle on y place un ressort. Cependant l’imprimer avec sa tige en une seule pièce aurait nécessité beaucoup de supports à l’impression. J’ai donc divisé la pièce en 3 parties avec filetage pour éviter l'ajout de supports et cela permet également d’insérer la tige dans son futur cadre en bois sur la planche. Le filament utilisé est du PLA imitation bois d’où la forte ressemblance avec du bois. Voici les pièces modélisées imprimées en 3D avant montage :



Et voici le tout assemblé (sans utiliser de vis ou de colle puisque tout se visse parfaitement grâce aux filetages).



Cette poignée m’a demandé beaucoup de temps car Fusion 360 n’est pas très adapté pour traiter des maillages avec beaucoup de points. J’ai donc dû faire le filetage à part puis l’importer dans blender pour l’insérer dans la poignée en comblant les trous dans la géométrie de la pièce. J’ai également appris à créer des filetages sur Fusion 360. Pour que les 2 pièces puissent se visser facilement après impression il est très important de modifier une des 2 pièces pour réduire l'épaisseur de son filetage (d’environ 1mm) car il y a des écarts de précisions entre une pièce usinée et l’impression en 3D.

**Pendant la séance :**

Pour commencer il a fallu découper la planche du jeu aux dimensions 414 x 800 x 0.5 cm qui correspondent à celles définies lors de l’élaboration de la maquette 3d. Cependant comme expliqué dans le compte rendu précédent, pour les bumpers nous avons besoin d’incruster de fines plaques métalliques à ras de la planche (permettant de détecter si la bille est à la fois en contact avec la plaque et le fil électrique du bumper), et notre planche est trop longue pour rentrer entièrement dans la découpeuse laser. Avec les conseils des gérants du FabLab nous avons décidé de coller 3 petites planches de bois d’une épaisseur de 3mm sur la grande planche afin de pouvoir graver chacune des planches au laser pour ensuite venir les coller sur la grande planche les unes à côté des autres.

Pour placer les capteurs infrarouges, nous utilisons une fine plaque de plexiglas posée à ras de la planche grâce à nouveau à une gravure. J’ai effectué des tests avec un capteur infrarouge en dessous de la plaque de plexiglas pour vérifier que la bille soit toujours détectée à travers la plaque transparente. La bille est correctement détectée si le capteur est positionné à ras de la plaque de plexiglass.

Puis j'ai déterminé les dimensions et la position de cette plaque en fonction de la position des séparateurs de colonnes (pièces noires en haut du flipper sur la maquette).
Redha a ensuite réalisé un fichier vectoriel svg sur Inkscape pour graver et perçer des trous dans la partie supérieure du flipper.

J’ai ensuite continué la modélisation de la maquette 3d du  pinball afin d’y dessiner le contour du flipper ainsi que la zone de lancement. Cela permettra de découper des morceaux de bois aux dimensions voulues plus facilement par la suite.
Pour cela je me suis aidé de différents schémas de construction de vrais flippers afin de créer les arrondis en haut du flipper qui permettront à la balle de sortir de la zone de lancement pour arriver dans la zone de jeu.

J’ai ensuite dessiné la rampe de sortie de billes, celle-ci doit permettre de diriger les billes jusqu’à la zone de lancement. Etant donné que la sortie de jeu des billes (située au niveau des flippers) est bien plus basse que l’emplacement de la bille avant lancement (juste au dessus de la tige de la poignée), nous avons décidé d’utiliser un solénoïde pour pousser la bille et l’amener jusqu’à la zone de lancement. Ce solénoïde sera déclenché à chaque sortie de bille (qui sera détectée grâce à un capteur infrarouge). Celui ci poussera la balle grâce au même bras imprimé en 3d utilisé dans l'ancien prototype du slingshot (pièce noire sur l'image ci dessous) et sera placé au niveau du trou en bas à droite de la maquette.



Finalement j’ai modélisé les pièces qui permettront de tendre l'élastique des slingshots en respectant la forme emblématique que l’on retrouve sur tous les flippers. Voici la modélisation sur Fusion 360 : 



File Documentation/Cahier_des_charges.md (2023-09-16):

# Cahier des charges du projet Flipper #

Notre objectif est de fabriquer un Flipper (Pinball en anglais) à l’aide d’une carte Arduino, de moteurs et de capteurs en moins de 3 mois.

Le principe de ce jeu est de marquer le plus de points possible en dirigeant une ou plusieurs billes métalliques sur un plateau vers des cibles interactives. Nous souhaitons intégrer les principaux composants d’un Flipper dans une version moins encombrante avec des composants abordables afin de rendre ce jeu accessible au plus grand nombre dans un projet open source. Ceci nous permettra de renforcer nos connaissances par la pratique, en apprenant à utiliser une grande variété d'outils et de composants, mais aussi d'acquérir des compétences en gestion de projets.

Les principales parties de notre Flipper seront :

* Une planche de bois.
* Les Flippers (petits leviers contrôlés par le joueur, qui permettent d'envoyer la bille sur les différents éléments du jeu).
* Boutons (permettent de contrôler les flippers).
* Bumpers (renvoient la balle dans la direction opposée et ajoutent des points au joueur).
* Slingshots (font rebondir la bille sur des élastiques munis de leviers mécaniques pour la repositionner dans la zone de jeu).
* Tige avec ressort munie d'une poignée (permettant de lancer la bille).
* Capteurs de passages (capteurs infrarouges permettant de savoir où la bille est passée afin d’ajouter des points ou de déclencher certains éléments de jeu).
* Des cibles (surfaces munies de "microswitches" permettant de détecter un contact afin de comptabiliser des points).
* Rampes que la bille peut emprunter pour marquer des points.
* Afficheur LCD (affiche le score, le nombre d'essais restants et des messages relatifs à la partie).
* Mode MultiBille (bonus relâchant plusieurs billes simultanément depuis la partie haute du flipper).
* Leds (décoration et interactivité du flipper, s’allument quand certains capteurs sont déclenchés).

Bonus s'il reste du temps : Une roue de la fortune déclenchée à certains moments de la partie (roue tournante permettant de gagner des points en fonction de la position d’arrêt de la roue).

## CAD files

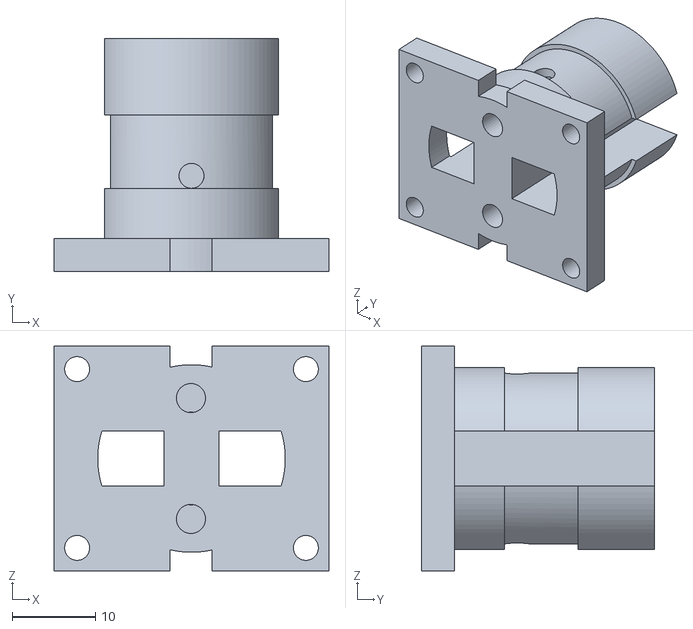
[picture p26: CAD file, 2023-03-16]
Modelisations 3D/bumper part2.stl
33.0 x 28.0 x 27.0

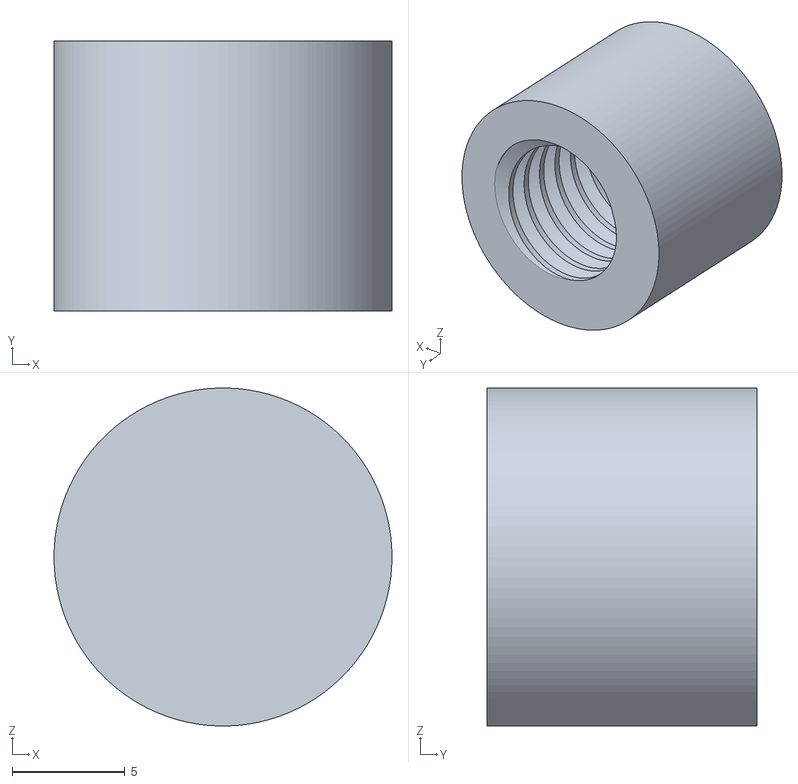
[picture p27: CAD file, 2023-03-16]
Modelisations 3D/Poignée embout v0.stl
15.0 x 12.0 x 15.0

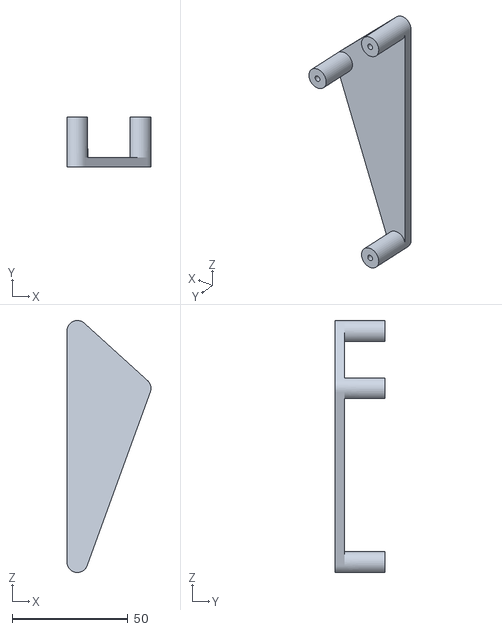
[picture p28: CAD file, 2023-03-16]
Modelisations 3D/Slingshot gauche tendeur version finale v6.stl
36.4 x 21.5 x 109.0

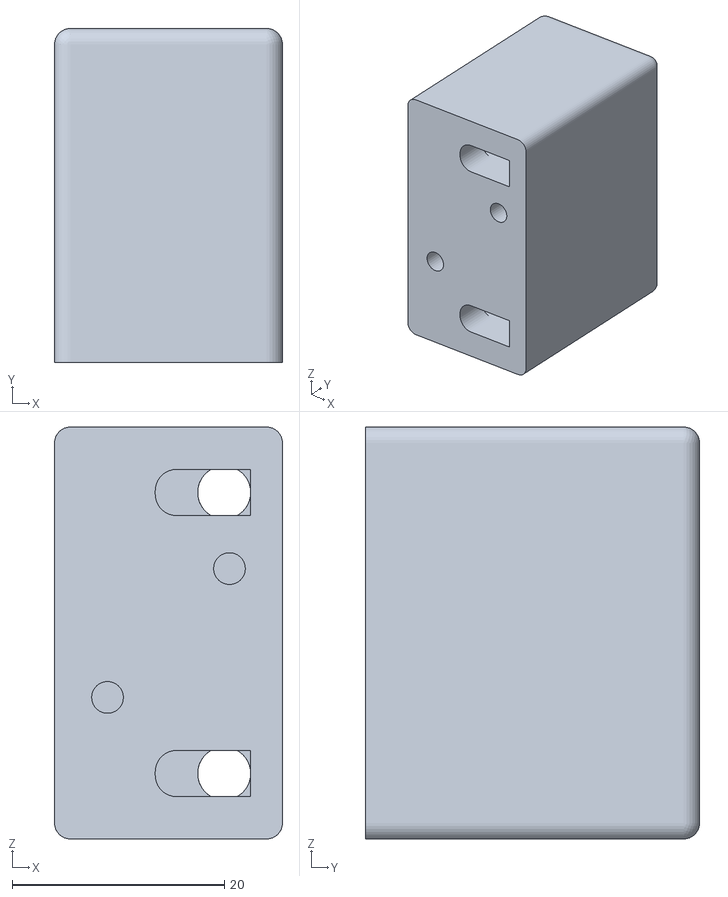
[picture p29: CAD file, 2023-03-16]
Modelisations 3D/Support 2 cibles flipper v3.stl
21.5 x 31.5 x 38.8

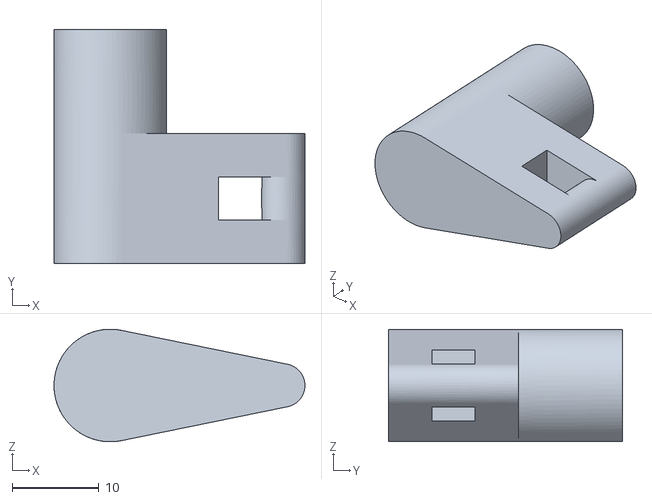
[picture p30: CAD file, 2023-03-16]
Modelisations 3D/flipper_bras v7.stl
29.0 x 27.0 x 13.0

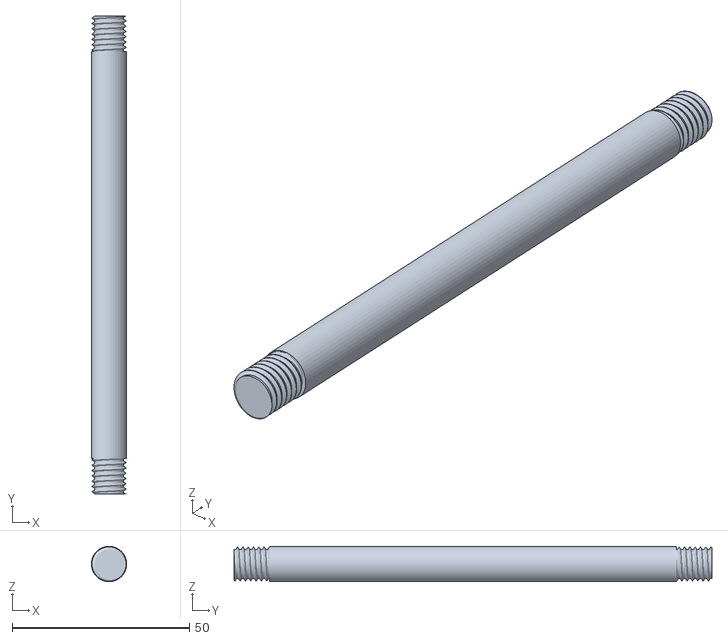
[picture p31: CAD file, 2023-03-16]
Modelisations 3D/tige_lanceur v3.stl
9.99 x 135.0 x 9.99

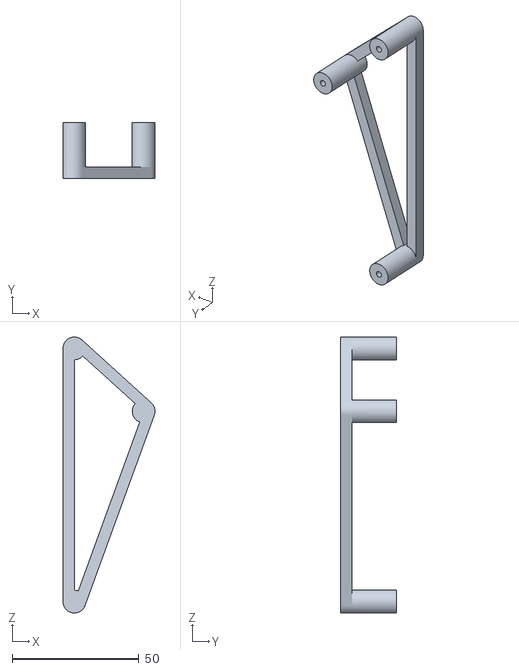
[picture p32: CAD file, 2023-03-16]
Modelisations 3D/Slingshot gauche positionnement microswitch v3.stl
36.4 x 22.0 x 109.0

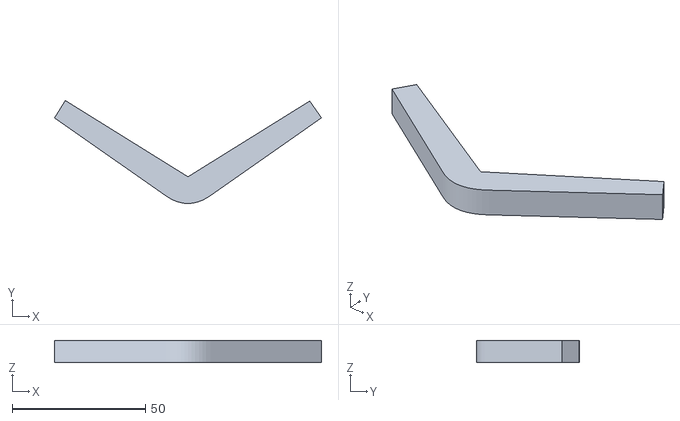
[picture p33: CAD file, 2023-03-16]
Modelisations 3D/orientation flipper.stl
100.0 x 38.6 x 8.33

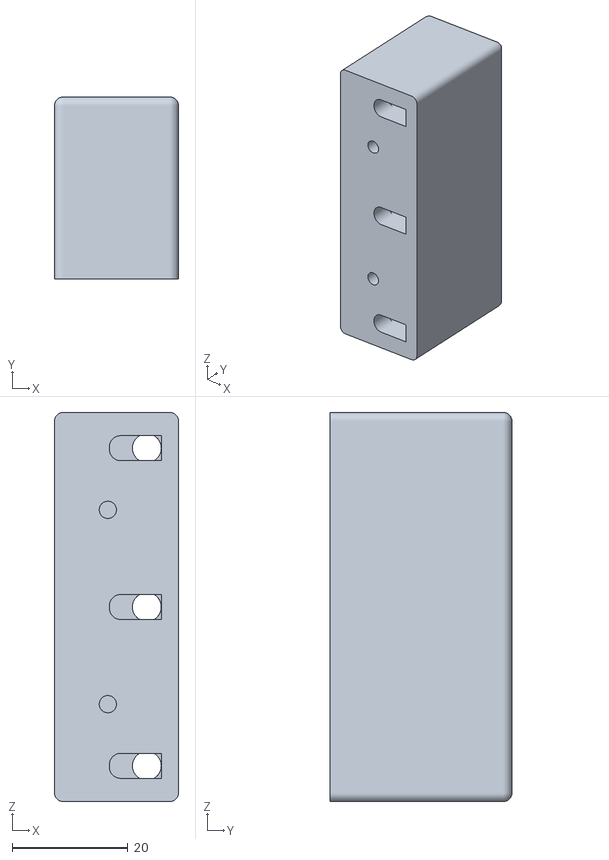
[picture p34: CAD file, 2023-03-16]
Modelisations 3D/Support cibles flipper v9.stl
21.5 x 31.5 x 67.3

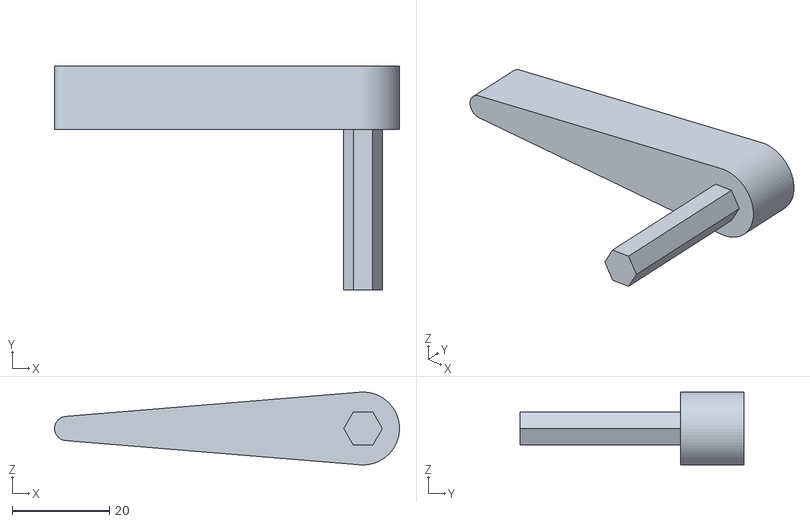
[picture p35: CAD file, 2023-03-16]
Modelisations 3D/flipper v2.stl
71.0 x 46.0 x 15.0

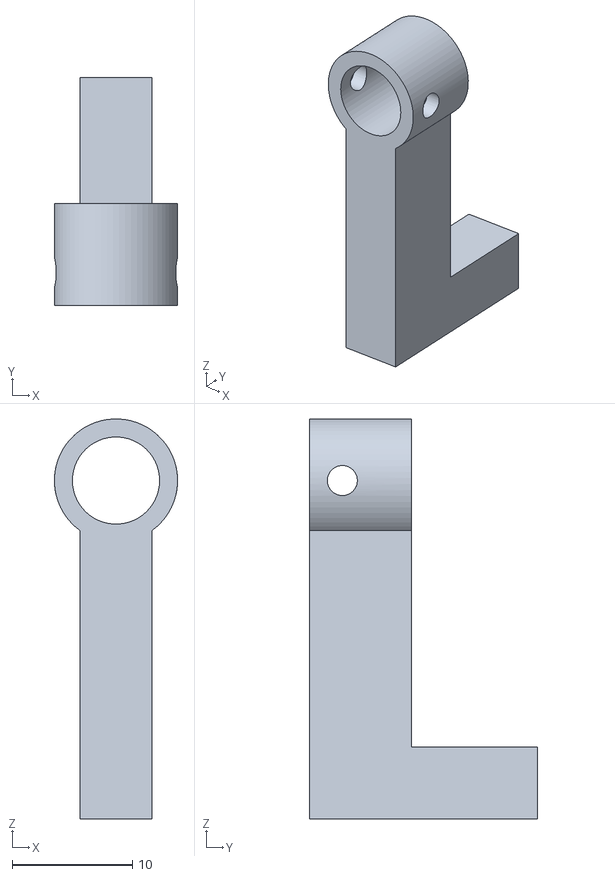
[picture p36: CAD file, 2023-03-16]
Modelisations 3D/Bras solenoide vers zone lancement v2.stl
10.2 x 19.0 x 33.3

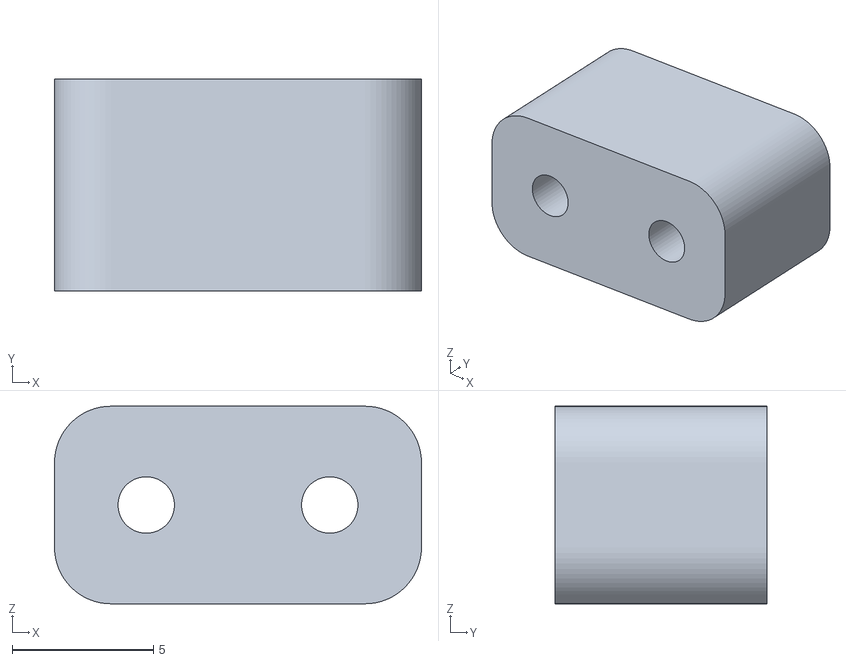
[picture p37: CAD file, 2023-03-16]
Modelisations 3D/support_microswitch_slingshot v2.stl
13.0 x 7.50 x 7.00

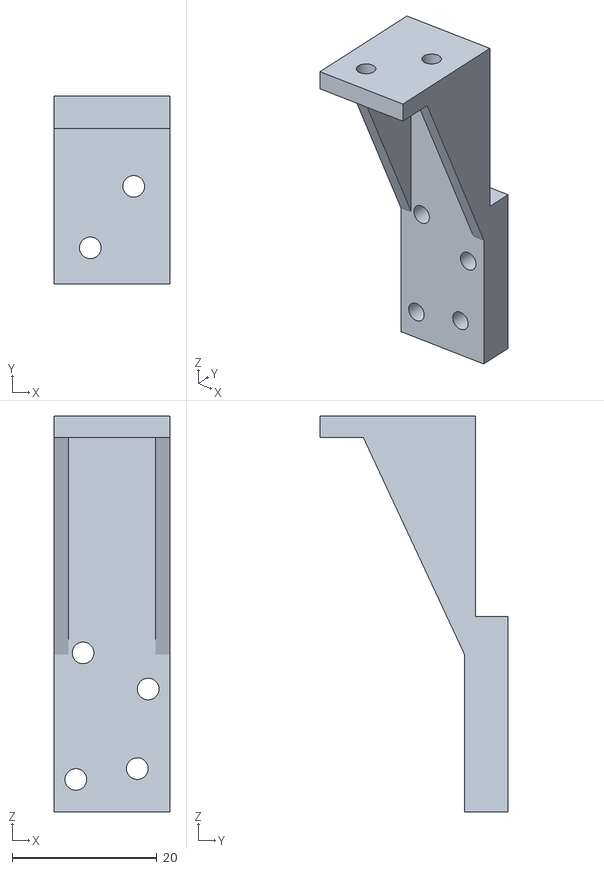
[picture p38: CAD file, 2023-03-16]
Modelisations 3D/Equerre_solenoide_bumper v9.stl
16.0 x 26.0 x 54.8

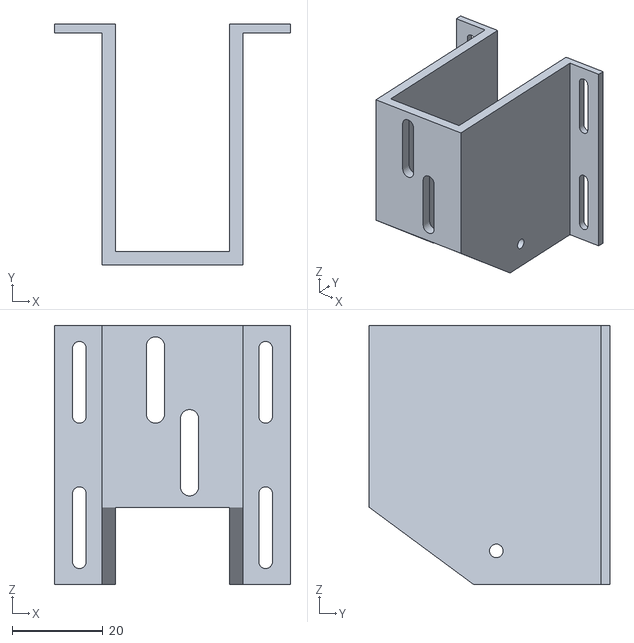
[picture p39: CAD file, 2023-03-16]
Modelisations 3D/Slingshot_levier_equerre v8.stl
52.0 x 53.0 x 57.0

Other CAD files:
Modelisations 3D/Support_capteur_infrarouge v3.stl
Modelisations 3D/Equerre solenoide zone lancement v2.stl
Modelisations 3D/Slingshot_levier_barre v8.stl
Modelisations 3D/Support 1 cible v2.stl
Modelisations 3D/Equerre solenoide flipper v3.stl
Modelisations 3D/Separateur_colonnes_pinball v2.stl
Modelisations 3D/bumper_pinballv3.stl
Modelisations 3D/cible v3.stl
Modelisations 3D/entree_rampe v8.stl
Modelisations 3D/flipper_attache_bras v7.stl

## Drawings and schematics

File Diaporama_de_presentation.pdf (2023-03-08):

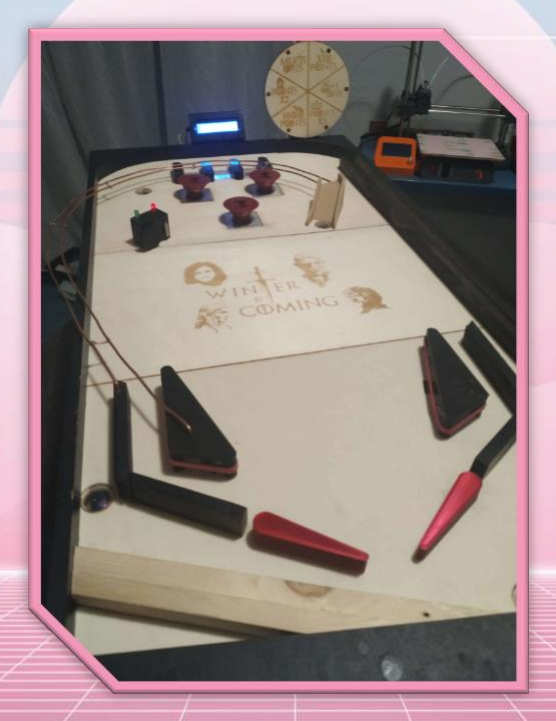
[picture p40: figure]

### PeiP2 Polytech Nice-Sophia Par Adrien Waeles-Devaux et Redha Abderrahmane

# Choix du projet et objectif

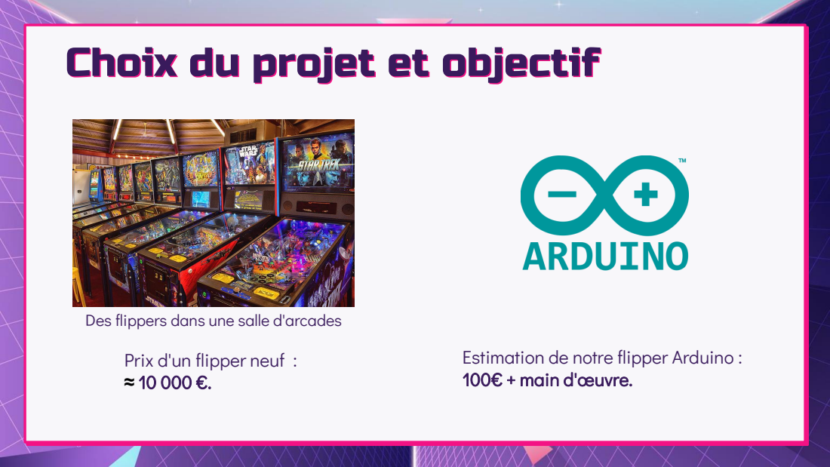
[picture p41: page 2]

Des flippers dans une salle d'arcades
Prix d'un flipper neuf :

Estimation de notre flipper Arduino :
100€ + main d'œuvre.

1

2

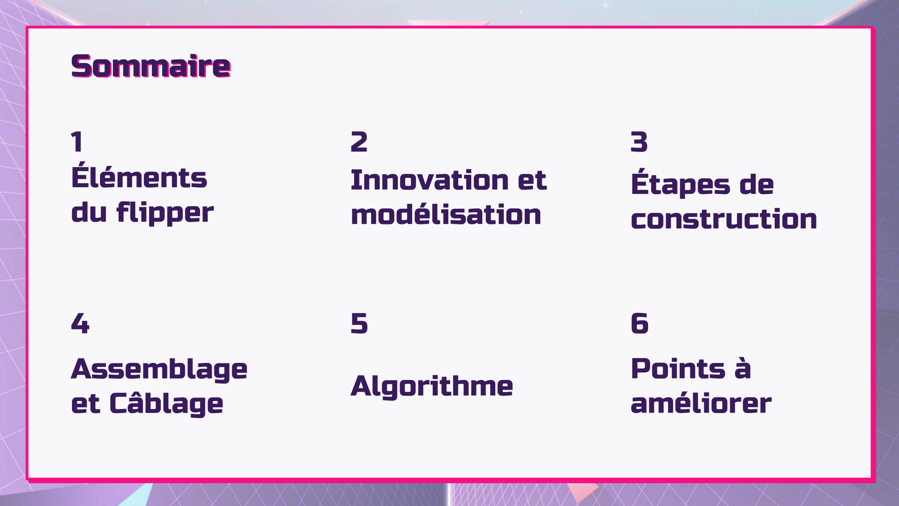
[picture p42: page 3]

## Éléments du flipper

## Innovation et modélisation

## Étapes de construction

3

## Assemblage et Câblage

4

## Algorithme

5

## Points à améliorer

6

## Sommaire

## 1 - Les éléments du flipper

### Capteur IR

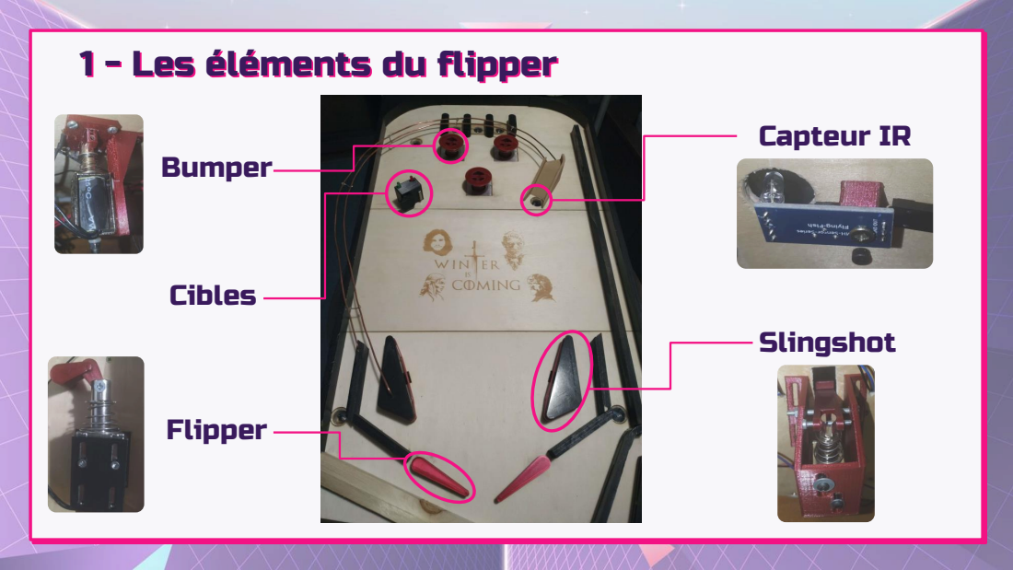
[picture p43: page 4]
Flipper; Bumper; Slingshot; Cibles

## 2 - Innovation et modélisation

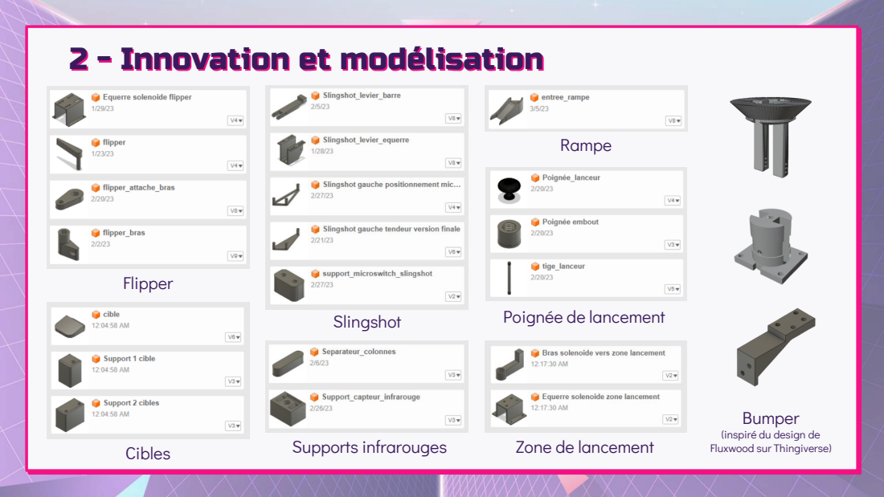
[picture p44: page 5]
Flipper; Slingshot; Poignée de lancement; Cibles; Supports infrarouges; Zone de lancement; Rampe

Bumper
(inspiré du design de
Fluxwood sur Thingiverse)

## 3 - Étapes de construction : Slingshot

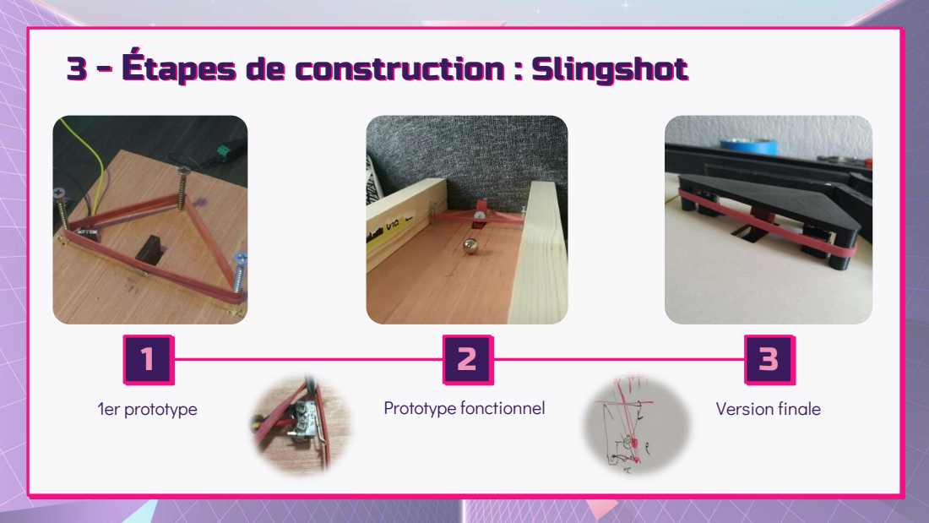
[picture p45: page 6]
1er prototype; Prototype fonctionnel; Version finale

## 3 - Étapes de construction: planche de jeu

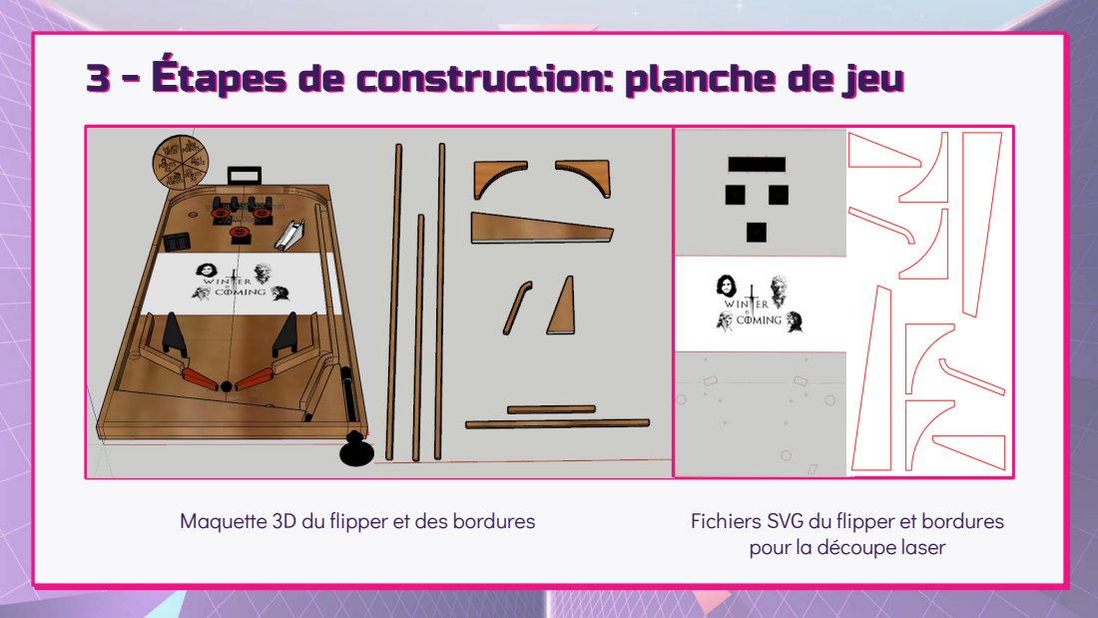
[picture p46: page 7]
Maquette 3D du flipper et des bordures; Fichiers SVG du flipper et bordures

pour la découpe laser

## 4 - Assemblage

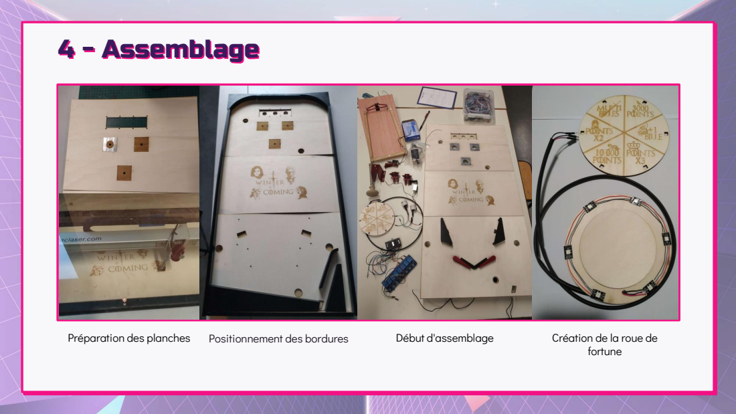
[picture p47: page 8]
Préparation des planches; Début d'assemblage; Création de la roue de; fortune

Positionnement des bordures

## 4 - Câblage du flipper

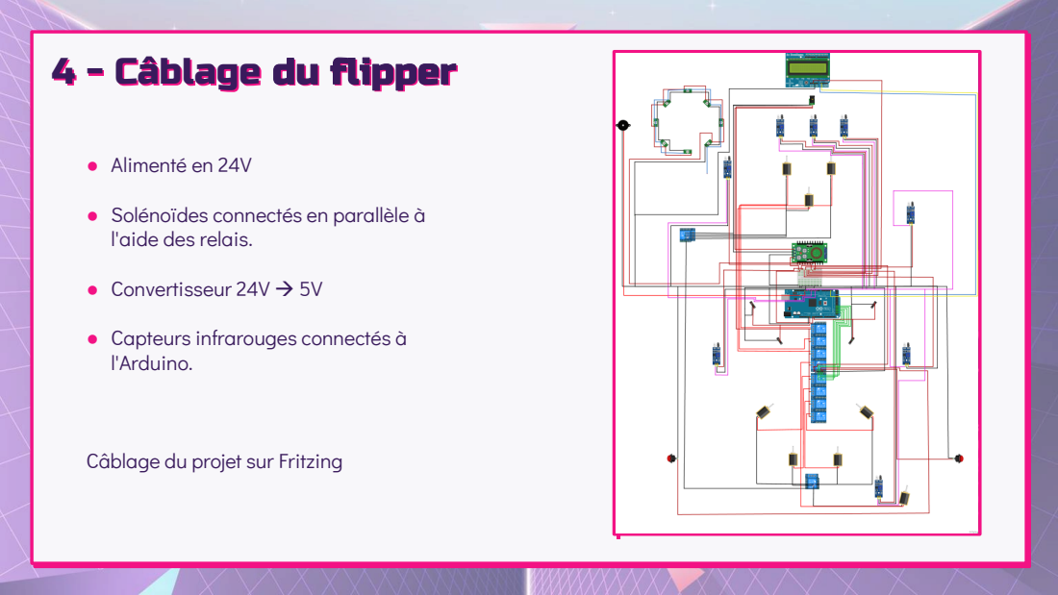
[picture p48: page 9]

● Alimenté en 24V
● Solénoïdes connectés en parallèle à
l'aide des relais.
● Convertisseur 24V → 5V
● Capteurs infrarouges connectés à
l'Arduino.

Câblage du projet sur Fritzing

## 5 – Algorithme : exemple

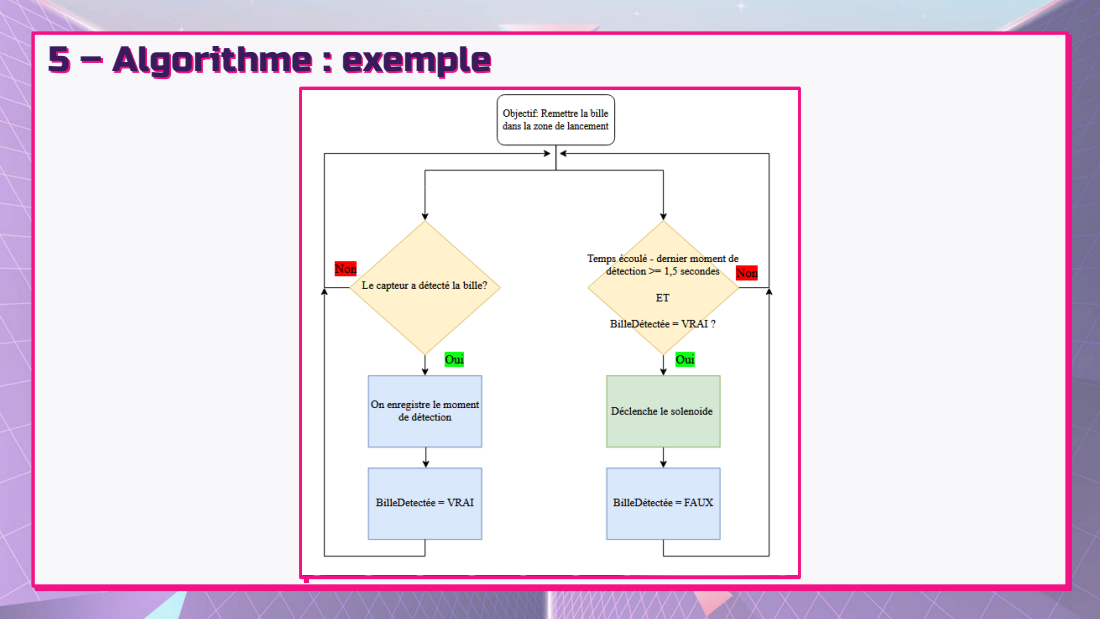
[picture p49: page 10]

## 6 - Points à améliorer

Difficultés et solutions | A suivre ….

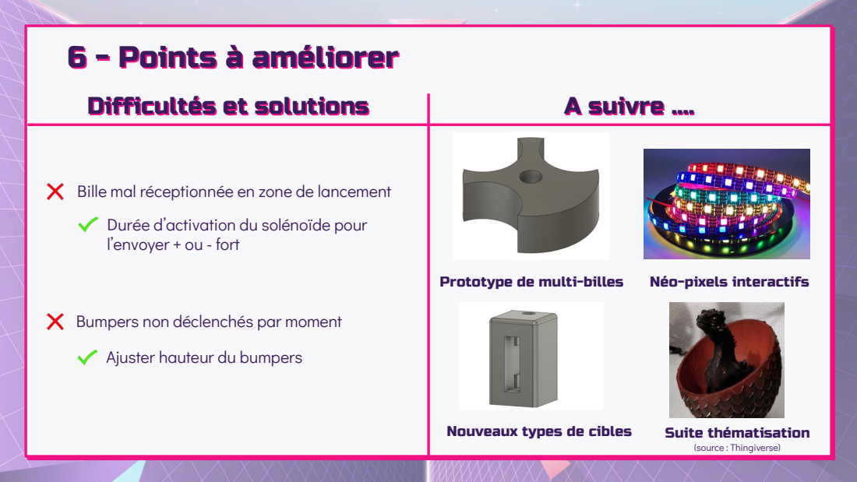
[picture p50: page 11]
Suite thématisation (source : Thingiverse)

Bille mal réceptionnée en zone de lancement
Durée d’activation du solénoïde pour
l’envoyer + ou - fort

Prototype de multi-billes

Néo-pixels interactifs

Bumpers non déclenchés par moment
Ajuster hauteur du bumpers

Nouveaux types de cibles

# CONCLUSION

### Un projet formateur

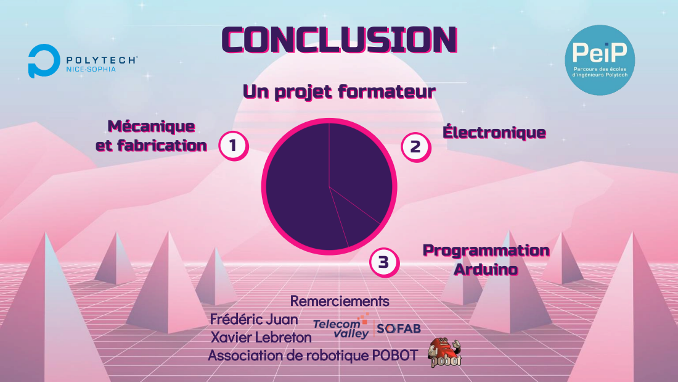
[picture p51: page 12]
Remerciements; Mécanique et fabrication; Électronique; Programmation Arduino

Frédéric Juan
Xavier Lebreton
Association de robotique POBOT







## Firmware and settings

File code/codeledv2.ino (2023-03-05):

const int MAX_LVL = 20;
const int lvl=1;
const int led_bleue = 2;
const int led_rouge = 3;
const int led_jaune = 4;
const int led_verte = 5;
const int bouton_bleu = 6;
const int bouton_rouge = 7;
const int bouton_jaune = 8;
const int bouton_vert = 9;
int valeurbouton_bleu;
int valeurbouton_rouge;
int valeurbouton_jaune;
int valeurbouton_vert;
int ordre[MAX_LVL];
int ma_combinaison[MAX_LVL];
int drapeau = 0;

void setup() {
  Serial.begin(9600);
  pinMode(bouton_bleu,INPUT);
  pinMode(bouton_rouge,INPUT);
  pinMode(bouton_jaune,INPUT);
  pinMode(bouton_vert,INPUT);
  pinMode(led_bleue,OUTPUT);
  pinMode(led_rouge,OUTPUT);
  pinMode(led_jaune,OUTPUT);
  pinMode(led_verte,OUTPUT);
  digitalWrite(led_bleue,HIGH);
  digitalWrite(led_rouge,HIGH);
  digitalWrite(led_jaune,HIGH);
  digitalWrite(led_verte,HIGH);
  debut_partie();
}

void sequence_hasard(){
  randomSeed(analogRead(0));
  for (int i=0; i<MAX_LVL; i++){
    ordre[i] = random(2,6);
  }
}

void suite_couleur(int lvl){
  for (int index=0; index<=lvl-1; index++){
      digitalWrite(ordre[index],LOW);
      delay(1000);
      digitalWrite(ordre[index],HIGH);
      delay(500);
  }
}

void jeu(){
  for (lvl=1; lvl<=MAX_LVL; lvl++){
      suite_couleur(lvl);
      delay(2000);
  }
}

void debut_partie(){
  sequence_hasard();
  jeu();
}

void mauvaise_sequence(){
}

void bonne_sequence(){
}

void loop() {
}

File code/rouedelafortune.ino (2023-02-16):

#include <Adafruit_NeoPixel.h>

int nombreLeds =6;
int nombreTours = 4;
int casefinale;
int tempsPause=150;

int buzzer=2;

Adafruit_NeoPixel strip = Adafruit_NeoPixel(nombreLeds, 6, NEO_GRB + NEO_KHZ800);

void setup() {
  pinMode(buzzer, OUTPUT);
  strip.begin();
  strip.show(); // Initialise toute les led à 'off'
  digitalWrite(2, HIGH);
}

void loop() {
  casefinale = random(0, nombreLeds);
  for(int tour=1; tour<nombreTours; tour++){
    for (int led=0; led<nombreLeds; led++){
      strip.setPixelColor(led, random(0, 22), random(0, 22), random(0, 22));
      strip.show(); // on affiche 
      tone(buzzer,1000,150);
      delay(tempsPause);
      noTone(buzzer);

      strip.setPixelColor(led, 0, 0, 0);
      strip.show();
    }
  }
  for (int led=0; led<casefinale; led++){
      strip.setPixelColor(led, random(0, 22), random(0, 22), random(0, 22));
      strip.show(); // on affiche
      tone(buzzer,1000,tempsPause);
      delay(tempsPause);
      digitalWrite(2, HIGH);
      strip.setPixelColor(led, 0, 0, 0);
      strip.show();
      tempsPause+=100;
  }
  for (int clignote=0; clignote<5; clignote++){
      strip.setPixelColor(casefinale, random(0, 22), random(0, 22), random(0, 22));
      strip.show(); // on affiche
      tone(buzzer,293,200);
      delay(200);
      digitalWrite(2, HIGH);
      strip.setPixelColor(casefinale, 0, 0, 0);
      strip.show();
      delay(800);
  }
  delay(2000);
  tempsPause = 150;
}

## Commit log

2022-12-13 Create Code Arduino
2022-12-13 Create Cahier des charges.md
    Description du projet avec quelques details sur les pieces utilisées
2022-12-13 Create repartition des taches.md
2022-12-14 Rename code Arduino to code_Arduino
2023-01-12 Add files via upload
    fichier de modélisation blender de la poignée de la zone de lancement
    [poignée_flipper.blend]
2023-02-16 Add files via upload
    J'ai supprimé le premier compte rendu car il y avait quelques erreurs
2023-03-02 V2: Correction de quelques erreurs
2023-09-16 Update Cahier des charges.md
2023-09-16 Update and rename repartition des taches.md to Répartition_des_tâches.md
2023-09-16 Rename Cahier des charges.md to Cahier_des_charges.md
